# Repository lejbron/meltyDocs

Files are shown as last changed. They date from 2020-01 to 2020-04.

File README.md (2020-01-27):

This project was created to put up together all stuff according to homemade version of Ultimaker Original.
All information you can find here is non-commercial and has only one goal - to simplify assembling process and streamline all necessary staff for printer usage.
I will be truly happy if this information can be useful for the community, please feel free to contact me if you have any questions according to this project.

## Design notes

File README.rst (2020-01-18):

Полезные ссылки
===============

Инструкции
----------

.. toctree::
   :titlesonly:
   :maxdepth: 4

   Исходная инструкция <http://plastmaska.ru/sobiraem-3d-printer-svoimi-rukami/>
   Настройка прошивки Marlin <https://3d-diy.ru/blog/3d-printery/nastrojka-proshivki-marlin/>

Software
--------

.. toctree::
   :titlesonly:
   :maxdepth: 4

   Printrun <https://github.com/kliment/Printrun>
   Slic3r <https://manual.slic3r.org/intro/overview>
   Marllin <https://github.com/MarlinFirmware/Marlin>

Магазины в Москве
-----------------

.. toctree::
   :titlesonly:
   :maxdepth: 4

   Ultrarobox <https://www.ultrarobox.ru/>
   Zona-3d <https://zona-3d.ru/>
   3d-diy <https://3d-diy.ru/>

Магазины в Санкт-Петербурге
---------------------------

.. toctree::
   :titlesonly:
   :maxdepth: 4

   fastnvr <https://fastnvr.ru/index.php?route=common/home>

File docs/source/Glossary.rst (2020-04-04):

:orphan:

.. _glossary:

=========
Глоссарий
=========

.. glossary::

  |Marlin|
    open-source проект универсальной прошивки 3D-принтера

  |MKS GEN|
    материнская плата управления 3D-принтером

  |MKS MINI|
    LCD дисплей с управлением и SD-cardreader, сделанный Makebase.

  |EEPROM|
    Electrically Erasable Programmable Read-Only Memory

  |A4988|
    Драйвер для шагового двигателя nema17

.. |Marlin| raw:: html

  <a href="https://marlinfw.org/docs/configuration/configuration.html" target="_blank">
  Marlin</a>

.. |MKS GEN| raw:: html

  <a href="https://reprap.org/wiki/MKS_GEN" target="_blank">
  MKS GEN 1.4</a>

.. |MKS MINI| raw:: html

  <a href="https://reprap.org/wiki/MKS_MINI_12864" target="_blank">
  MKS MINI 12864</a>

.. |EEPROM| raw:: html

  <a href="https://marlinfw.org/docs/features/eeprom.html" target="_blank">
  EEPROM</a>

.. |A4988| raw:: html

  <a href="https://3d-diy.ru/wiki/arduino-moduli/drajver-shagovogo-dvigatelya-a4988/" target="_blank">
  A4988</a>

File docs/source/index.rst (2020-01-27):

MeltyDIY
========

.. toctree::
   :caption: Guides
   :titlesonly:
   :maxdepth: 4

   Guides/Melty-AssemblingGuide
   Configure/conf_index
   Guides/Melty-Calibration
   Guides/Melty-Troubleshooting

* :ref:`BOM`
* :ref:`glossary`

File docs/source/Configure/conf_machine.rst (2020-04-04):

Настройка маханических параметров
=================================

Концевые выключатели
--------------------

В этом разделе необходимо задать используемые на плате порты:

.. include:: MARLIN_R2D2\Configuration.h
   :code: C++
   :start-line: 569
   :end-line: 579

При необходимости инвертировать конецевые выключатели измените следующие
константы:

.. include:: MARLIN_R2D2\Configuration.h
   :code: C++
   :start-line: 605
   :end-line: 614

Драйверы шаговых моторов
------------------------

Необходимо непорседственно указать модель используемых дравйров шаговых
двигателей :term:`A4988`.
MARLIN_R2D2

.. include:: MARLIN_R2D2\Configuration.h
   :code: C++
   :start-line: 614
   :end-line: 643

Настройка перемещения по осям
-----------------------------

Шаги перемещения
~~~~~~~~~~~~~~~~

Оси X и Y
``````````

- Шаговый двигатель: 200 шагов на оборот, 16 микро-шагов на шаг (ПЕРЕМЫЧКИ)
- Приводной ремень GT2: шаг 2мм
- Шкив: 20 зубьев

Сколько шагов должен совершить двигатель, чтобы по оси X и Y было совершено
перемещение ровно в 1 мм:

(200*16)/(2*20) = 80

Ось Z
``````

- Мотор с интегрированным трапецеидальным винтом:

  - Диаметр 8 мм
  - Шаг 2 мм
  - Заходность 4

  Количество шагов: (200*16)/(2*4) = 400

.. include:: MARLIN_R2D2\Configuration.h
   :code: C++
   :start-line: 681
   :end-line: 688

Ограничение максимальной скорости перемещения
---------------------------------------------

.. include:: MARLIN_R2D2\Configuration.h
   :code: C++
   :start-line: 688
   :end-line: 695

Ускорение перемещения по осям
-----------------------------

.. include:: MARLIN_R2D2\Configuration.h
   :code: C++
   :start-line: 695
   :end-line: 703

Изменение направления вращения моторов
--------------------------------------

При необходимости изменить напрвление моторов измените следующие константы:

.. include:: MARLIN_R2D2\Configuration.h
   :code: C++
   :start-line: 945
   :end-line: 950

Homing
------

.. include:: MARLIN_R2D2\Configuration.h
   :code: C++
   :start-line: 969
   :end-line: 975

Указание размера области печати
-------------------------------

.. include:: MARLIN_R2D2\Configuration.h
   :code: C++
   :start-line: 977
   :end-line: 989

Отступ по оси Z
---------------

.. include:: MARLIN_R2D2\Configuration.h
   :code: C++
   :start-line: 279
   :end-line: 286

Automatic Bed Leveling
----------------------

1. Первый шаг:

.. include:: MARLIN_R2D2\Configuration.h
   :code: C++
   :start-line: 790
   :end-line: 796

2. Второй шаг:

.. include:: MARLIN_R2D2\Configuration.h
   :code: C++
   :start-line: 1050
   :end-line: 1094

3. Третий шаг:

.. include:: MARLIN_R2D2\Configuration.h
   :code: C++
   :start-line: 1210
   :end-line: 1222

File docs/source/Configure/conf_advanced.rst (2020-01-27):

Расширенные настройки Marlin
============================

Изменение этих натсроек не всегда необходимо, но о них полезно помнить.

Thermal Protection
------------------

В некоторых случаях необходимо увеличить периоды ожидания механизмов термальной
защиты.

.. code-block:: c++

  #if ENABLED(THERMAL_PROTECTION_HOTENDS)
    #define THERMAL_PROTECTION_PERIOD 80        // Seconds
    #define THERMAL_PROTECTION_HYSTERESIS 8     // Degrees Celsius

.. code-block:: c++

  #define WATCH_TEMP_PERIOD 40                // Seconds
  #define WATCH_TEMP_INCREASE 4               // Degrees Celsius

.. code-block:: c++

  #if ENABLED(THERMAL_PROTECTION_BED)
    #define THERMAL_PROTECTION_BED_PERIOD 40    // Seconds
    #define THERMAL_PROTECTION_BED_HYSTERESIS 4 // Degrees Celsius

    /**
     * As described above, except for the bed (M140/M190/M303).
     */
    #define WATCH_BED_TEMP_PERIOD 120                // Seconds
    #define WATCH_BED_TEMP_INCREASE 2               // Degrees Celsius
  #endif

Controller Fan
--------------

Extruder coolong Fan
--------------------

.. code-block:: c++

  #define E0_AUTO_FAN_PIN 10

Quick Home
----------

.. code-block:: c++

  #define QUICK_HOME                     // If homing includes X and Y, do a diagonal move initially

Babystepping
------------

.. code-block:: c++

  #define BABYSTEPPING

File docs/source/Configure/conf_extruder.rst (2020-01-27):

Экструдер
=========

Количество экструдеров
----------------------

.. code-block:: c++

  #define EXTRUDERS 1

Диаметр филамента по умолчанию
------------------------------

.. code-block:: c++

  #define DEFAULT_NOMINAL_FILAMENT_DIA 3.0

Настройка подачи филамента
--------------------------

.. code-block:: c++

  #define PREVENT_COLD_EXTRUSION
  #define EXTRUDE_MINTEMP 170

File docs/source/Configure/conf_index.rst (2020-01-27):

Настройка :term:`Marlin`
========================

.. toctree::
  :titlesonly:
  :maxdepth: 5

  conf_general
  conf_extruder
  conf_temperature
  conf_machine
  conf_advanced

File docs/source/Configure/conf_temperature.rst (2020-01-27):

Температурные настройки
=======================

Термистор стола
---------------

Зависит от *термистора стола*.

.. code-block:: c++

  #define TEMP_SENSOR_BED 1

Ограничения минимальной температуры
-----------------------------------

.. code-block:: c++

  #define HEATER_0_MINTEMP   5
  #define HEATER_1_MINTEMP   5
  #define HEATER_2_MINTEMP   5
  #define HEATER_3_MINTEMP   5
  #define HEATER_4_MINTEMP   5
  #define HEATER_5_MINTEMP   5
  #define BED_MINTEMP        5

Ограничения максимальной температуры
------------------------------------

.. code-block:: c++

  #define HEATER_0_MAXTEMP 275
  #define HEATER_1_MAXTEMP 275
  #define HEATER_2_MAXTEMP 275
  #define HEATER_3_MAXTEMP 275
  #define HEATER_4_MAXTEMP 275
  #define HEATER_5_MAXTEMP 275
  #define BED_MAXTEMP      150

PID settings
------------

Необходимо настраивать в процессе калибровки

.. code-block:: c++

  #define DEFAULT_Kp 21.68
  #define DEFAULT_Ki 2.00
  #define DEFAULT_Kd 58.61

Защита нагрева сопла
--------------------

https://marlinfw.org/docs/gcode/M302.html

.. code-block:: c++

  #define PREVENT_COLD_EXTRUSION
  #define EXTRUDE_MINTEMP 170

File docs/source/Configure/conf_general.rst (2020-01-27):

Общие настройки
===============

Имя автора
----------

.. code-block:: c++

  #define STRING_CONFIG_H_AUTHOR "lejbron" // Who made the changes.

Скорость запсиси
----------------

Зависит от выбранной материнской платы. Для :term:`MKS GEN` = 250000.

.. code-block:: c++

  #define BAUDRATE 250000

Материнская плата
-----------------

.. code-block:: c++

  #ifndef MOTHERBOARD
    #define MOTHERBOARD BOARD_MKS_GEN_13
  #endif

Название принтера
-----------------

.. code-block:: c++

  #define CUSTOM_MACHINE_NAME "Melty"

Настройка EEPROM
----------------

Подробное описание включения :term:`EEPROM`.

Дисплей
-------

Для указания используемого дисплея (:term:`MKS MINI`) необходимо изменить
следующие константы:

.. code-block:: c++

  #define DISPLAY_CHARSET_HD44780 CYRILLIC

.. code-block:: c++

  #define LCD_FEEDBACK_FREQUENCY_DURATION_MS 0 //2
  #define LCD_FEEDBACK_FREQUENCY_HZ 0 //5000

И раскомментировать следующие константы:

.. code-block:: c++

  #define SDSUPPORT

.. code-block:: c++

  #define MKS_MINI_12864

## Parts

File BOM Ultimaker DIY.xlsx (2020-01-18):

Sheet: Main
Корпус
 | Винт M3*16 | 40
 | Гайка M3 | 40
 | Концевик (X Y) | 2 |  | https://fastnvr.ru/
 | Винт M2.5*16 | 4
 | Гайка M2.5 | 4
 | Разъем для кабеля с предохранителем и выключателем | 1 |  | https://zona-3d.ru/
 | Винт М3*10 | 2
 | Гайка М3 | 2
 | Светодиодная лента + питание + управление |  |  | IKEA
Механика
 | F688(ZZ) | 8 |  | https://zona-3d.ru/
 | Медная втулка (с графитовыми вставками) | 4 |  | https://zona-3d.ru/
 | Корпус каретки (UM2-SliderBlock-B11mm.stl) | 4
 | Пружины для ремней | 4 |  | https://fastnvr.ru/
 | Ремень GT2 закольцованный 305 зубов 610мм | 4 |  | https://fastnvr.ru/
 | Вал 8мм | 2 | 348 | https://www.ultrarobox.ru/
 | Вал 8мм | 2 | 337 | https://www.ultrarobox.ru/
 | Двойная шпуля GT2 20 зубов 8мм | 1 |  | https://fastnvr.ru/
 | Шпуля GT2 20 зубов 8мм | 8 |  | https://fastnvr.ru/
 | spacer 5mm stl | 2
 | spacer 10mm stl | 4
 | spacer 20mm stl | 1
 | Ремень GT2 закольцованный 100 зубов 200мм | 2
 | Шпуля GT2 20 зубов 5мм | 2 |  | https://fastnvr.ru/
 | Nema 17 (X Y) | 2 |  | https://fastnvr.ru/
 | motor original.stl | 2
 | Винт М3*25 | 8
 | Шайба кузовная и широкая | 8 |  | https://www.ultrarobox.ru/
 | e3d mount.stl
 | LM6LUU | 2
 | Вал 6мм | 1 | 300.5 | https://www.ultrarobox.ru/
 | Вал 6мм | 1 | 320 | https://www.ultrarobox.ru/
Основание стола
 | Основа стола из аллюминия | 1 |  | https://www.ultrarobox.ru/
 | LMK12LUU | 2 |  | https://www.ultrarobox.ru/
 | Гайка от трапециидальной пары | 1 |  | https://fastnvr.ru/
 | Винт М3*12 | 8
 | Винт М3*10 | 4
 | Гайки М3 | 12
 | Деревянные заглушки | 2
 | Винт М3*16 | 4
 | Гайка М3 | 4
 | Вал 12мм | 2 | 339 | https://zona-3d.ru/
Ось Z
 | Nema 17 с интг. трапециидальным винтом | 1 |  | https://fastnvr.ru/
 | Демпфер двигателя | 1
 | Винт М3*5 | 2
 | Винт М3*8 | 2
 | Винт М3*40 (или меньше) | 2
 | Гайка М3 | 6
 | Концевик (Z) | 1
 | Винт М2,5*20 | 2
 | Гайка М2,5 | 2
Завершение стола
 | Нагревательный эелемет MK3 | 1 |  | https://www.ultrarobox.ru/
 | Термистор стола | 1 |  | https://www.ultrarobox.ru/
 | Провод сечением 2,5 кв.мм. L=1,2 м. | 2
 | Винт М3*30 | 3
 | Гайки самоконтрящие М3 | 3
 | Гайки регулирования стола | 1 |  | https://fastnvr.ru/
 | Стекло | 4
 | Канцелярские зажимы
Экструдер
 | Nema 17 | 1 |  | https://fastnvr.ru/
 | Подающая шестерня | 1 |  | https://fastnvr.ru/
 | extruder 1 v2.stl
 | 623ZZ | 1 |  | https://fastnvr.ru/
 | Винт M3*10 | 1
 | фитинг | 1
 | extruder 2.stl | 1
 | extruder 3.stl | 1
 | e3d mount.stl | 1
 | e3d clamp.stl | 1
 | e3d fan.stl | 1
 | Винт М3*12 | 1
 | Винт М3*35 | 3
 | HotEnd e3d v6 |  |  | https://fastnvr.ru/
Электроника
 | Блок питаня 350Вт 12В | 1 |  | https://www.ultrarobox.ru/
 | MKS GEN 1.4 | 1 |  | https://fastnvr.ru/
 | Дисплей MKS MINI 12864 LCD V 1.0 | 1 |  | https://www.ultrarobox.ru/
 | Турбинный куллер | 1 |  | https://www.ultrarobox.ru/
 | Контролер нагрева MKS MOSFET | 1 |  | https://zona-3d.ru/
 | Кулер охлаждения детали | 2
 | Провода
 | Термоусадки
 | Гибкая оплётка кабеля
 |  | 1
 | Пневмофитинг | 1 |  | https://fastnvr.ru/
 | Радиатор экструдера | 1 |  | https://fastnvr.ru/
 | Термобарьер | 1 |  | https://fastnvr.ru/
 | MK8 механизм протяжки нити (правый рычаг) | 1 |  | https://fastnvr.ru/

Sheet: Крепёж
Винт | M3x10 | 30 | шт.
Винт | M3x12 | 30 | шт.
Винт | M3x14 | 15 | шт.
Винт | M3x16 | 85 | шт.
Винт | M3x20 | 20 | шт.
Винт | M3x25 | 20 | шт.
Винт | M3x30 | 21 | шт. | Винт M3x30 21 шт.
Винт | M3x4 | 2 | шт. | Винт M3x4 2 шт.
Винт | M3X5 | 10 | шт. | Винт M3X5 10 шт.
Винт | M3X6 | 10 | шт. | Винт M3X6 10 шт.
Винт | M3X45 | 2 | шт. | Винт M3X45 2 шт.
Винт | M3x8 | 10 | шт. | Винт M3x8 10 шт.
Гайка | M2,5 | 6 | шт. | Гайка M2,5 6 шт.
Гайка | M3 | 130 | шт. | Гайка M3 130 шт.
Гайка самоконтрящаяся | M3 | 35 | шт. | Гайка самоконтрящаяся M3 35 шт.
Шайба | M2,5 | 6 | шт. | Шайба M2,5 6 шт.
Шайба кузовная или широкая | M3 | 17 | шт. | Шайба кузовная или широкая M3 17 шт.

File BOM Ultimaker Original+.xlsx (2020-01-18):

 | Ultimaker Original+ |  |  | lasercut parts
 |  |  |  | injection moulded parts
Total quantity parts | 662
Partnummer |  | Naam | Quantity
1002 | A | Front Panel | 1
1003 | A | Back Panel | 1
1004 | A | Left Panel | 1
1005 | A | Right Panel | 1
1006 | A | Top Panel | 1
1007 | A | Bottom Panel | 1
1008 | A | Reel Holder Part A | 1
1009 | A | Reel Holder Mounting Plate | 1
1010 | A | Velcro parts | 4
1011 | A | Y-linear shaft | 2
1012 | A | X-linear shaft | 2
1016 | A | Feeder Quick Fit Coupling | 1
1017 | A | Feeder Motor | 1
1018 | A | Feeder Base Plate Motor Side | 1
1021 | A | Ball Bearing 688-2RS | 10
1023 | A | Limit Switch, Black Long Wire | 1
1025 | A | Limit Switch, Blue Wire | 1
1026 | A | Limit Switch, Red Wire | 1
1028 | A | Z-linear Shaft | 2
1029 | A | Bearing Cap Outside | 8
1031 | A | Feeder Bolt Clip | 1
1032 | A | Feeder Clamp A | 1
1033 | A | Feeder Clamp C | 1
1034 | A | Feeder Clamp B | 1
1035 | A | Feeder Lever | 1
1036 | A | Feeder Wheel | 1
1037 | A | Print Head Coupling Plate | 1
1039 | A | Feeder U bar | 1
1041 | A | Feeder Small Gear | 1
1044 | A | Z-shaft Cap Top | 2
1045 | A | Bearing Cap Inside | 6
1046 | A | Print Head Shaft X,Y | 2
1048 | A | Print Head Hot End Holder | 1
1049 | A | Aluminum Heater Block | 1
1053 | A | Hot End Isolator Tube | 1
1054 | A | Nozzle 0.4mm | 1
1055 | B | Hot End Isolator Coupler | 1
1056 | B | Sintered Bushing | 4
1057 | B | Z-shaft Cap Bottom | 2
1058 | B | Print Head Back | 1
1059 | B | Print Head Top Cap | 1
1061 | B | Print Head Bottom Cap | 1
1062 | B | Print Head Left | 1
1063 | B | Print Head Front | 1
1064 | B | Print Head Right | 1
1065 | A | Linear Bearing LM6LUU | 2
1067 | A | PEEK Isolator | 1
1069 | A | Tube Coupling Collet | 1
1071 | A | Clamp Clip | 2
1082 | A | X,Y-Motor | 2
1084 | A | Timing Pulley 5mm Shaft | 2
1085 | A | Timing Belt B100 MXL | 2
1086 | A | Timing Belt B300 MXL | 4
1088 | A | Timing Pulley 8mm Shaft | 10
1089 | A | Right Side Controller | 1
1091 | B | Main Board V2.1.1 | 1
1092 | A | Left Side Controller | 1
1093 | A | Bottom Cover Controller | 1
1095 | A | Top Cover Controller | 1
1097 | A | Spiral Sleeve | 1
1116 | A | Reel Holder Part B | 4
1117 | A | Sliding Block Part A | 8
1118 | A | Sliding Block Part B | 1
1119 | A | Sliding Block Part C | 2
1121 | A | Sliding Block Part D | 4
1122 | A | Sliding Block Part E | 1
1126 | A | Feeder Middle Plate | 1
1128 | A | Feeder Big Gear | 1
1129 | A | Knob | 1
1131 | A | Cable Duct Front | 2
1132 | A | Cable Duct Back | 2
1133 | A | Feeder Knurled Bolt | 1
1134 | A | Capnut M8 | 1
1136 | A | Washer M8 | 2
1137 | A | Nut M8 | 1
1139 | A | Spacer, White, 3.2x5x16 | 4
1142 | A | Ball Bearing 693ZZ | 1
1143 | A | Feeder Spring D2110 | 1
1144 | A | USB Cable | 1
1146 | A | Ultipanel Rev 1.1 | 1
1152 | A | Table Spring D2150 | 3
1154 | A | Print Table Glass | 1
1155 | A | Print Table Heated Bed | 1
1159 | A | Z-Motor with Trapezoidal Lead Screw | 1
1170 | A | Square Flanged Linear Bearing LMK12LUU | 2
1171 | A | Double flat Cable 10 Wire | 1
1183 | B | Heated Bed Cable | 1
1185 | A | PT100 B sensor | 1
1187 | A | Trapezoidal Lead Nut | 1
1201 | B | Washer Large M3 | 14
1202 | B | ISO 7380 M3x10 | 23
1203 | B | ISO 7380 M3x12 | 11
1204 | B | ISO 7380 M3x16 | 75
1205 | B | ISO 7380 M3x14 | 7
1206 | B | ISO 7380 M3x20 | 12
1207 | B | ISO 7380 M3x25 | 12
1208 | B | ISO 7380 M3x30 | 16
1209 | B | Nut M3 | 110
1211 | A | Set Screw M4x4 | 12
1214 | A | ISO 7040 Nut M3 Prev. torque A2 | 25
1217 | A | ISO 7380 M4x10 A2 | 8
1225 | A | tape | 1
1226 | A | grease | 1
1227 | A | Hex Key Screwdriver 2 | 1
1228 | A | pritt | 1
1238 | A | Power Adapter 24v-220W | 1
1241 | A | Motor Spacer | 2
1243 | A | Heated Bed Cable Clip | 1
1250 | A | SD card 4G | 1
1256 | A | Build Platform Glass Retainer Back | 4
1257 | A | Knurled Nut Platform | 3
1266 | C | Bowden tube | 1
1288 | A | Washer M6 | 3
1315 | A | Jumper | 2
1326 | A | Warning sticker | 1
1348 | A | Bolt M3x4 | 2
1362 | A | Tap Fix 2.5x14 mm staal verzinkt bolkop porzidrive | 2
1355 | B | Heated Bed Bolt 8 mm
1356 | B | Heated Bed Bolt 20 mm
1402 | A | Hex Key Wrench 2.5 | 1
1501 | D | Print Head Fancap Metal | 1
1502 | A | Spacer 3.2x6x8 | 8
1503 | A | Sliding Block Part F | 8
1504 | A | Sliding Block Part G | 4
1505 | A | print table cap | 1
1506 | A | print table cap side A | 1
1507 | A | print table cap side B | 1
1508 | A | print table cap middle | 2
1509 | A | Feeder cap | 1
1510 | A | Feeder wheelcap | 1
1511 | A | Short reel holder part A | 2
1512 | A | Print Head Fan 24VDC | 1
1513 | A | Heater Cartridge 24V 40W | 1
1514 | A | Metal Cable Clamp | 1
1522 | A | ulticontroller window | 1
1524 | B | copper grease | 1
1528 | A | Feeder Plate Non Motor Side | 1
1529 | A | Electronics Cover Plate | 1
1530 | A | X-Y calibration sticks | 2
1540 | A | Nylon M3 nut | 10
1541 | A | Nylon M3x 12 Panhead | 6
1542 | A | Nylon M3x 25 Panhead | 4
1545 | A | Spacer 3.2x6x3 | 2
1680 | A | Print Head Thumb screw 62mm | 4
1681 | A | Timingbelt spring | 4
1805 | 01 | Power Cable EU Type C13 CE
1806 | 01 | Power Cable UK Type C13 CE
1807 | 01 | Power Cable AU Type C13 CE
1808 | 01 | Power Cable US Type C13 CE
1818 | B | Print Table Base Plate | 1
Reserve onderdelen
1201 | B | Washer Large M3 | 5
1202 | B | ISO 7380 M3x10 | 5
1203 | B | ISO 7380 M3x12 | 5
1204 | B | ISO 7380 M3x16 | 5
1205 | B | ISO 7380 M3x14 | 5
1206 | B | ISO 7380 M3x20 | 5
1207 | B | ISO 7380 M3x25 | 5
1208 | B | ISO 7380 M3x30 | 5
1209 | B | Nut M3 | 10
1211 | A | Set Screw M4x4 | 5
1214 | A | ISO 7040 Nut M3 Prev. torque A2 | 10
1215 | A | ISO 10642 M3x8 A2 | 2
1216 | A | ISO 10642 M3x20 A2 | 2
1217 | A | ISO 7380 M4x10 A2 | 2
1540 | A | Nylon M3 nut | 2
1541 | A | Nylon M3x 12 Panhead | 2
1542 | A | Nylon M3x 25 Panhead | 2

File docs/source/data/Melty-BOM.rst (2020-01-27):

:orphan:

.. _BOM:

Перечень деталей для сборки MeltyDIY
====================================

.. csv-table:: **Детали**
 :header: "Деталь", "Наименование", "Ключевые харакстеристики"
 :widths: 4, 4, 10

 "Материнская плата", ":term:`MKS GEN`", "Скорость записи - 250000"

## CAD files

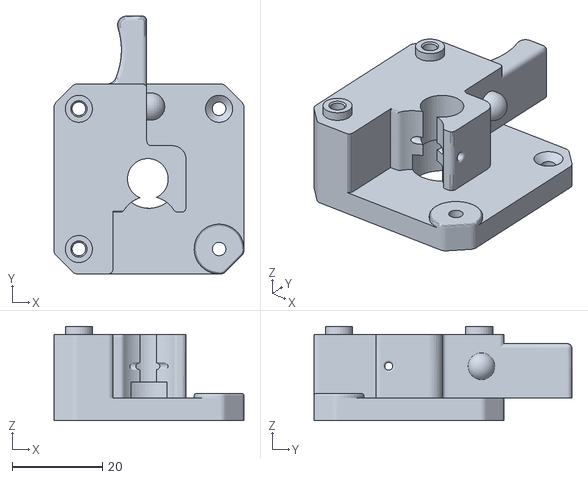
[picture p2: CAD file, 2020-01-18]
Пластиковые детали/extruder main.stl
42.0 x 57.0 x 20.8

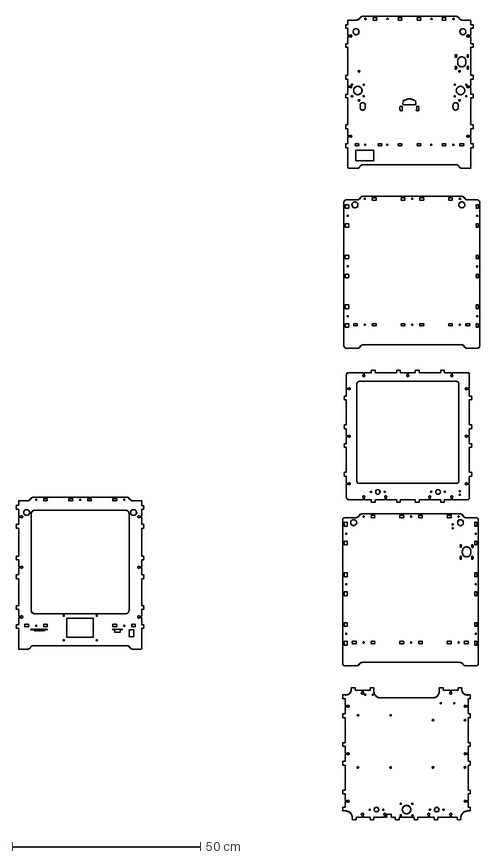
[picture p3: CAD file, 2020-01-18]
Корупс/Корпус для экрана mks tft28 sbase dual 6mm.dxf
122.9 x 213.2 cm

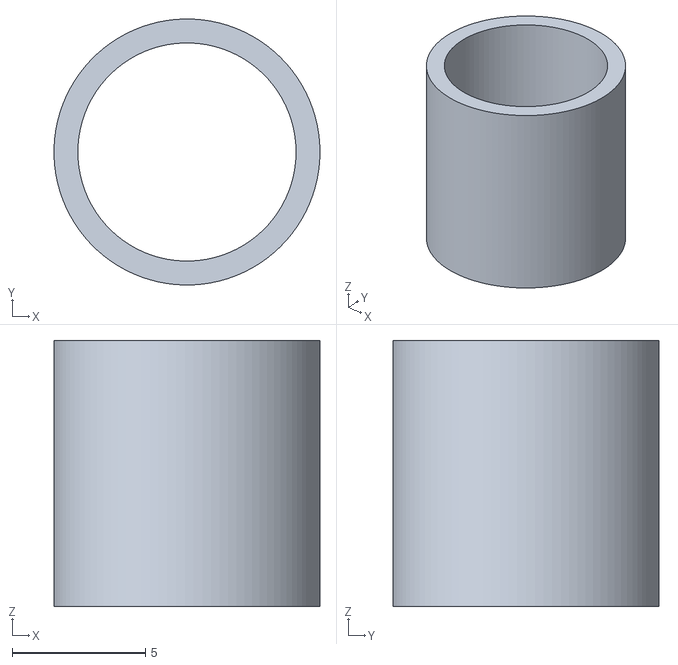
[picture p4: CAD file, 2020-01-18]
Пластиковые детали/spacer 10mm x4.stl
10.00 x 10.00 x 10.0

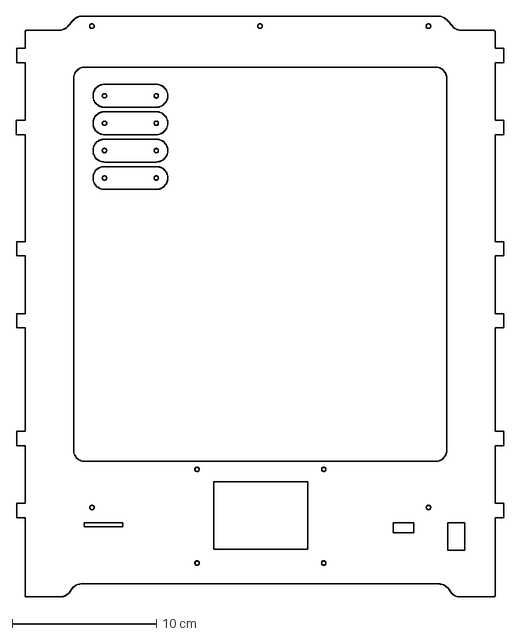
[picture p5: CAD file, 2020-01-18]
Корупс/Корпус для экрана mks tft28 sbase dual 3mm.dxf
33.8 x 40.3 cm

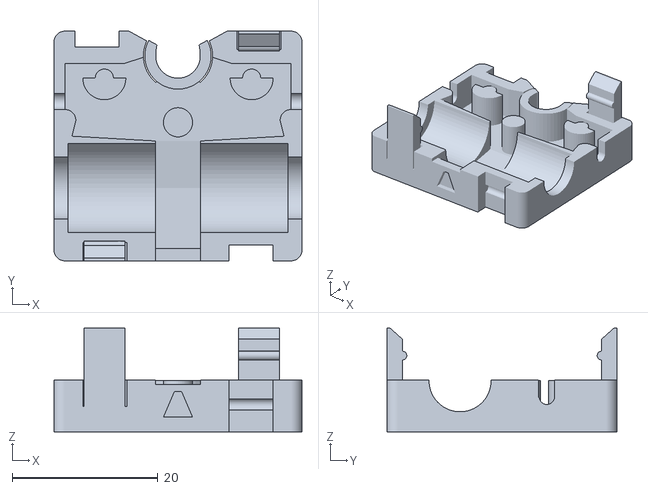
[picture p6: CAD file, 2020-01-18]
Пластиковые детали/UM2-SliderBlock-B12mm.stl
34.0 x 31.5 x 14.2

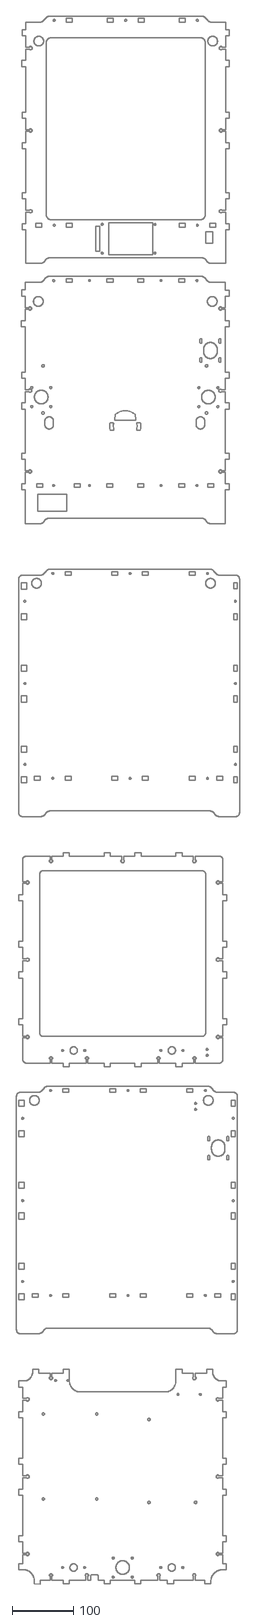
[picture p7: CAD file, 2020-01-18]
Корупс/Корпус для экрана mks mini 12864 6mm.dxf
363.6 x 2556.1

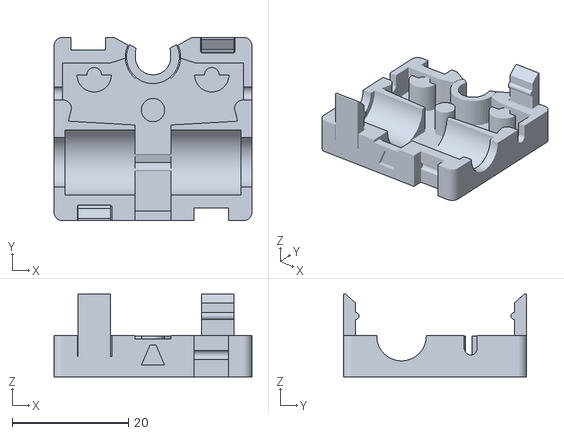
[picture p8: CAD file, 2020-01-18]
Пластиковые детали/UM2-SliderBlock-B11mm.stl
34.0 x 31.5 x 14.2

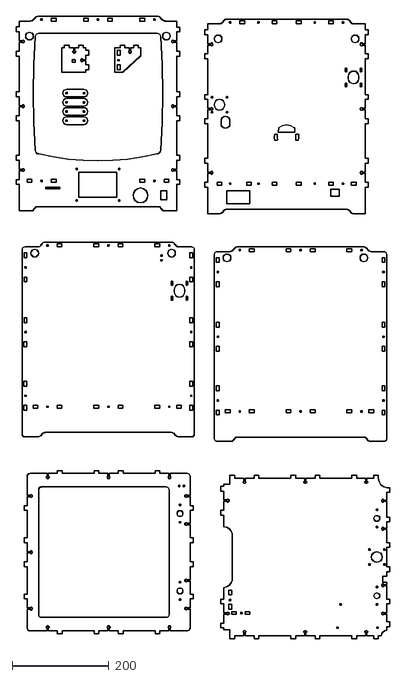
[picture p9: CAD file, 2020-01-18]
Корупс/Корпус для экрана 12864.dxf
773.8 x 1289.4

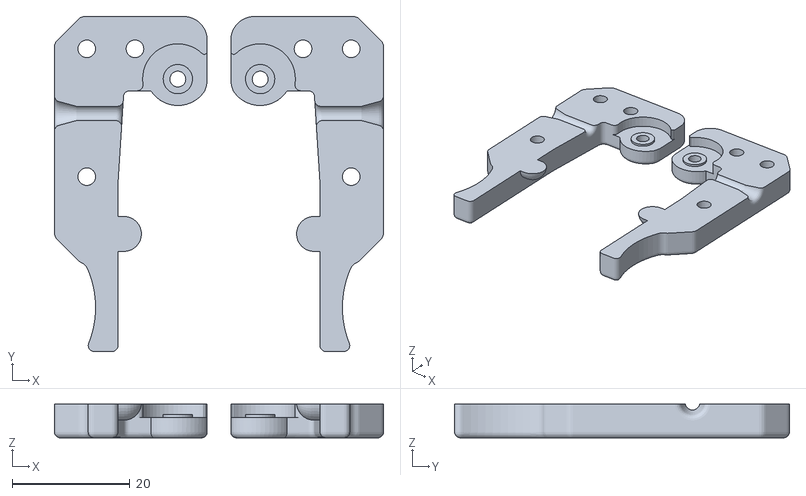
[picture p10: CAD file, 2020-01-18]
Пластиковые детали/extruder 1 v2.stl
56.0 x 57.0 x 5.75

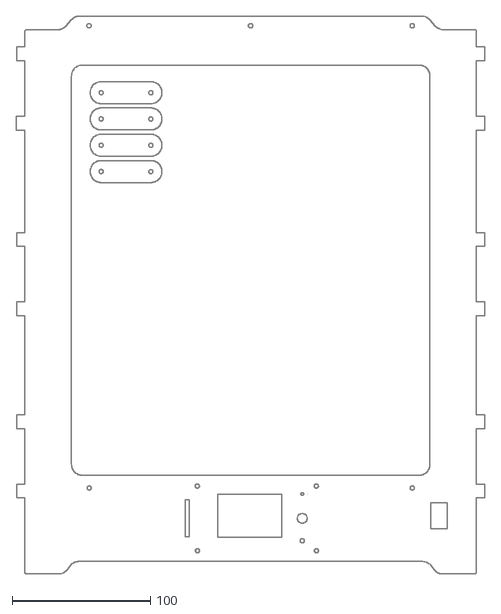
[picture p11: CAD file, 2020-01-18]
Корупс/Корпус для экрана mks mini 12864 3mm.dxf
338.4 x 403.3

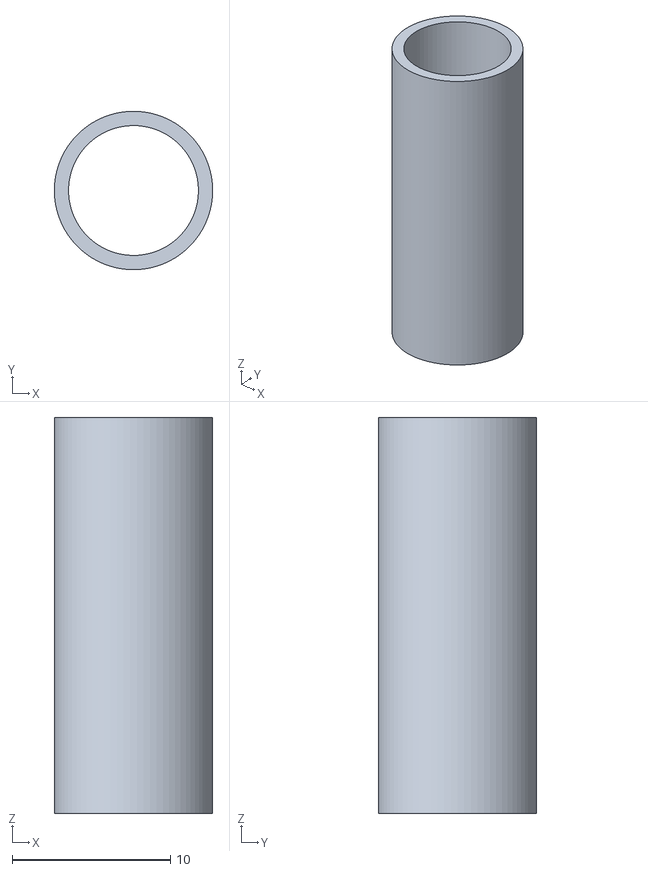
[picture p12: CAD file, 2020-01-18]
Пластиковые детали/spacer 20mm x1.stl
10.0 x 9.99 x 25.0

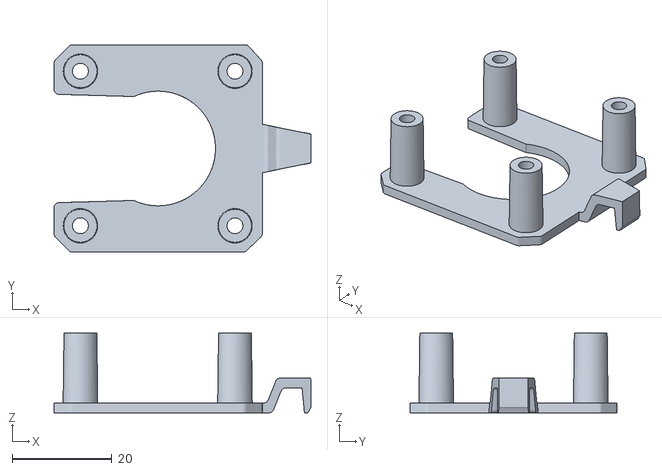
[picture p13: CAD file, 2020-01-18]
Пластиковые детали/motor original.stl
51.6 x 41.6 x 16.0

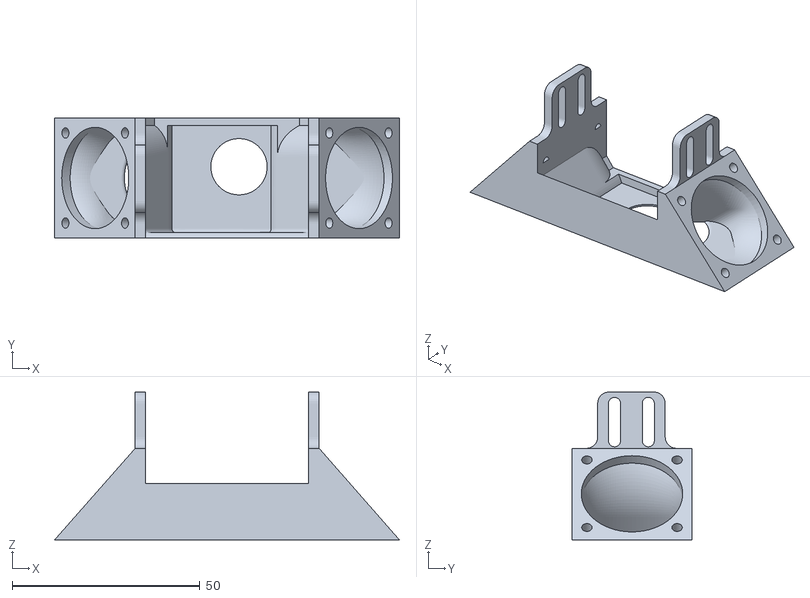
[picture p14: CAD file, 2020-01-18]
Пластиковые детали/e3d fan.stl
91.9 x 32.0 x 39.4

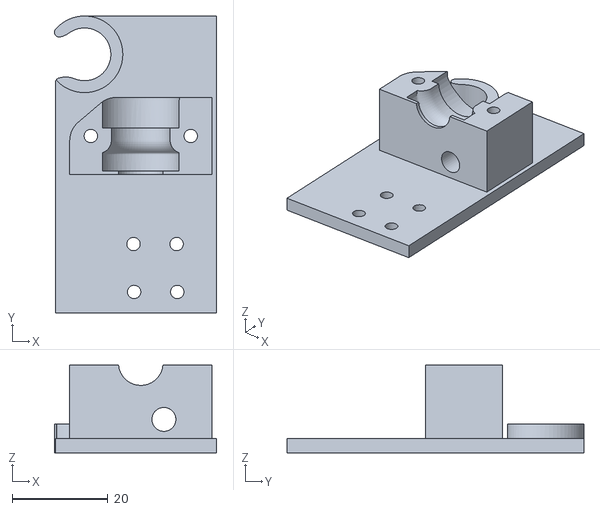
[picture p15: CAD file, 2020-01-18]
Пластиковые детали/e3d clamp.stl
33.9 x 62.0 x 18.4

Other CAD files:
Пластиковые детали/UM2-SliderBlock-B11mm-Uni.stl
Пластиковые детали/extruder 2.stl
Пластиковые детали/e3d mount.stl
Пластиковые детали/UM2-SliderBlock-B12mm-Uni.stl
Корупс/Корпус для экрана MKS TFT32.skp
Пластиковые детали/extruder 1 v1.stl
Пластиковые детали/spacer 5mm x2.stl

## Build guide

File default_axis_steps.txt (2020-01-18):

#define NEMA17_FULL_STEPS 200.0
#define NEMA17_MICROSTEPS 16.0
#define NEMA17_MOTOR_STEPS (NEMA17_FULL_STEPS * NEMA17_MICROSTEPS)
#define PULLEY_PITCH 2.0 //шаг ремня GT2
#define PULLEY_TEETH 20.0 //количество зубьев ремня GT2
#define Z_ROD_PITCH 2 //шаг резьбы трапецеидального винта = (длина участка в мм/количество витков)
 
#define WADE_PULLEY_TEETH 11.0
#define WADE_GEAR_TEETH 45.0
#define HOBBED_BOLT_DIAM 6.0 //диаметр подающей шестерни

#define XY_STEPS (NEMA17_MOTOR_STEPS / (PULLEY_PITCH * PULLEY_TEETH))

#define Z_STEPS (NEMA17_MOTOR_STEPS / Z_ROD_PITCH)
//Трапецеидальный винт диаметром 8 мм с шагом 2 мм  и заходностью 4: 200*16/2*4=400

#define WADE_GEAR_RATIO (WADE_GEAR_TEETH / WADE_PULLEY_TEETH)
#define HOBBED_BOLD_CIRC (M_PI * HOBBED_BOLT_DIAM) 

#define WADE_E_STEPS (NEMA17_MOTOR_STEPS * WADE_GEAR_RATIO / HOBBED_BOLD_CIRC)

#define DEFAULT_AXIS_STEPS_PER_UNIT   { XY_STEPS, XY_STEPS, Z_STEPS, ENG2_E_STEPS }

Steps per Unit (Extruder) = Motor Steps per Revolution * Extruder Gear Ratio / (Pinch Wheel Diameter * Pi)

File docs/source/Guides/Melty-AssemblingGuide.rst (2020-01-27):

Инструкция по сборке MeltyDIY
=============================

Сборка E3D v6
-------------

https://www.matterhackers.com/articles/how-to-assemble-an-e3d-v6-all-metal-hotend

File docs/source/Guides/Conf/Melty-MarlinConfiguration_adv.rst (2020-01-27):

Thermal Protection
==================

В некоторых случаях необходимо увеличить периоды ожидания механизмов термальной
защиты.

.. code:: C++

  #if ENABLED(THERMAL_PROTECTION_HOTENDS)
    #define THERMAL_PROTECTION_PERIOD 80        // Seconds
    #define THERMAL_PROTECTION_HYSTERESIS 8     // Degrees Celsius

.. code:: C++

  #define WATCH_TEMP_PERIOD 40                // Seconds
  #define WATCH_TEMP_INCREASE 4               // Degrees Celsius

.. code:: C++

  #if ENABLED(THERMAL_PROTECTION_BED)
    #define THERMAL_PROTECTION_BED_PERIOD 40    // Seconds
    #define THERMAL_PROTECTION_BED_HYSTERESIS 4 // Degrees Celsius

    /**
     * As described above, except for the bed (M140/M190/M303).
     */
    #define WATCH_BED_TEMP_PERIOD 120                // Seconds
    #define WATCH_BED_TEMP_INCREASE 2               // Degrees Celsius
  #endif

Controller Fan
==============

Extruder coolong Fan
====================

.. code:: C++

  #define E0_AUTO_FAN_PIN 10

Quick Home
==========

.. code:: C++
  #define QUICK_HOME                     // If homing includes X and Y, do a diagonal move initially

Babystepping
============

.. code:: C++

  #define BABYSTEPPING

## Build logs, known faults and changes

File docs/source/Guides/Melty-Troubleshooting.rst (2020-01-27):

Troubleshooting
===============

Отключить Buzzer
----------------

В файле :code:`pins_MKS_GEN_12.h` изменить следующую константу:

.. code-block:: c++

  #define BEEPER_PIN       -1

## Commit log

2020-01-18 added parts, BOM and note
    [BOM Ultimaker DIY.xlsx, BOM Ultimaker Original+.xlsx, UM2-SliderBlock-B11mm-Uni.stl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]
2020-01-27 Docs reworked. Marlin configuration part started. Glossary added.
